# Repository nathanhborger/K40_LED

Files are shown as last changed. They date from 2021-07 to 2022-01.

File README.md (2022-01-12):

# K40_LED
LED Ring Origin Light for K40 Laser.
This device was designed with the intention to provide a solution to the K40's lack of origin detection/positioning.
Placed at the back of the laser, and reflected through two mirrors, the light will shine on the working peice, making a very distinct appearance which simplifies and enables the user to identify the exact locatin of the laser head.

## Schematic


## PCB Layout


## PCB
thumbnail_IMG_0565

## Parts List
| QTY | PART | NOTES |
|:---:|:----:|:-----:|
|8|LED XLAMP COOL WHITE 5000K 2SMD|https://cree-led.com/media/documents/XLampMX3.pdf|
|13|RES 13 OHM 1% 1/8W 0805||
|4|IC LED DRIVER LIN 1.5A 8SOPWRPAD|https://www.ti.com/general/docs/suppproductinfo.tsp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|
|1|LED DRIVER CC BUCK 2-52V 350MA|https://www.meanwellusa.com/upload/pdf/LDD-H/LDD-H-spec.pdf|
|4|RES SMD 1 OHM 1% 1/8W 0805||
|4|CAP CER 0.011UF 50V C0G/NP0 0805	||
|5|CAP CER 1UF 16V X7R 0805||
|1|RES SMD 51.1 OHM 1% 1/8W 0805||

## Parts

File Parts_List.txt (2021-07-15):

K40_LED_PARTS-LIST

12V 1A Supply:
https://www.amazon.com/R-Tech-UL-Listed-Switching-Supply-Adapter/dp/B00FEOB4EI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

LEDS:

RESISTOR:
https://www.digikey.com/en/products/detail/vishay-dale/CRCW0805200RJNEAHP/5326891

SWITCH:

VERSION 2:

RESISTOR[]
https://www.digikey.com/en/products/detail/stackpole-electronics-inc/RMCF0805JT18R0/1711894

LEDS[]
https://www.digikey.com/en/products/detail/samsung-semiconductor-inc/SPMWH1228FD5WATUS3/5959071

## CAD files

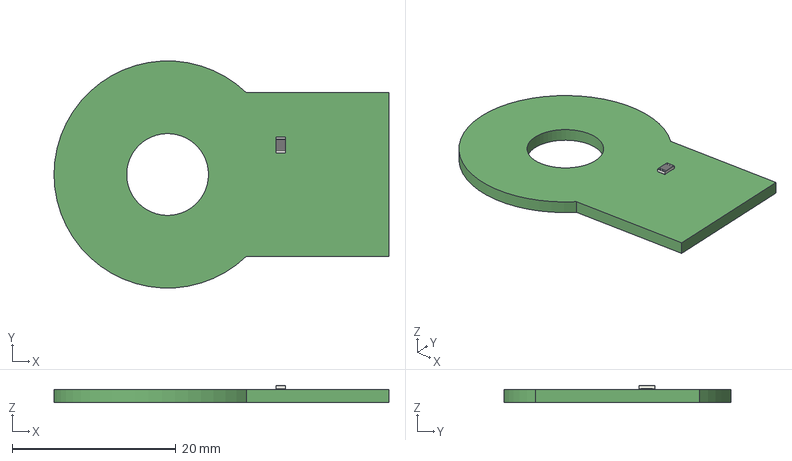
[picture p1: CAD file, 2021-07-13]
Fusion360_MODEL/K40-LED_PCB.step
41.0 x 27.7 x 2.10 mm

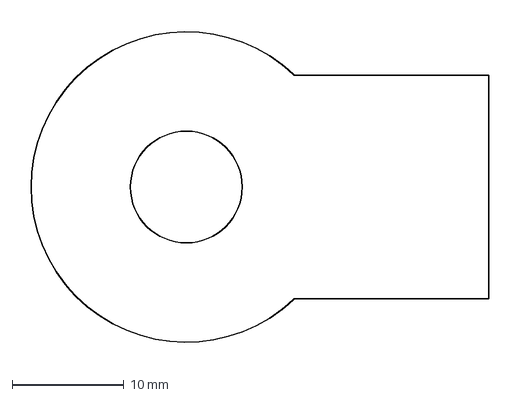
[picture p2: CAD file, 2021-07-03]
K40-LED_PCB/K40_LED_DXF.dxf
42.3 x 30.6 mm

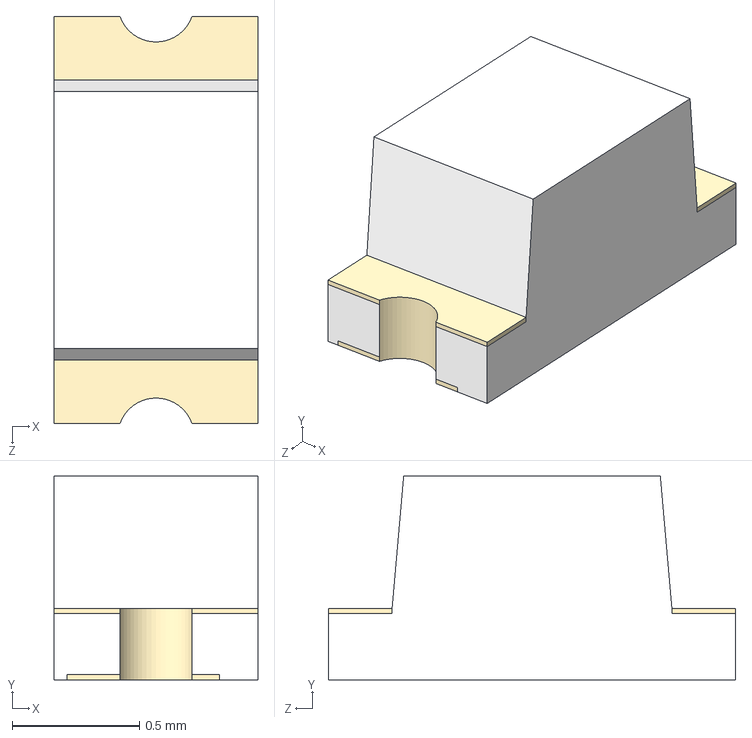
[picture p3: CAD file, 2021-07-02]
LRST-C190KGKT/LTST-C190KGKT.step
0.8 x 0.8 x 1.60 mm

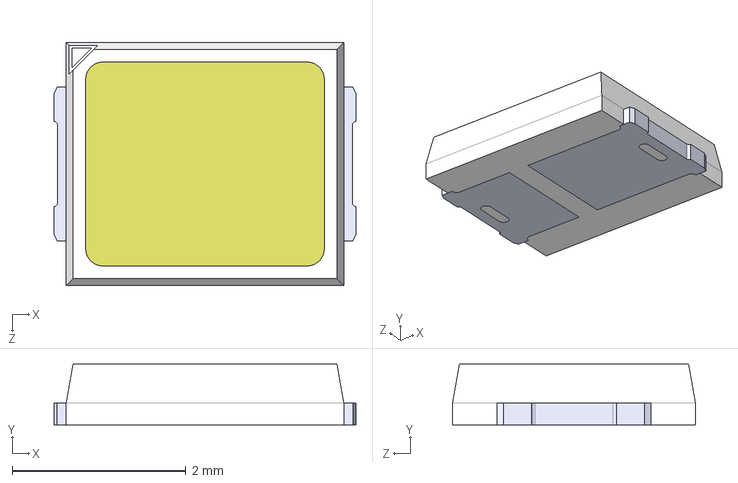
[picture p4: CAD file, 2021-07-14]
SPMWH1228FD5WATUS3_FOOTPRINT/LED_SPMWH1228FD5WARMSE.step
3.48 x 0.7 x 2.80 mm

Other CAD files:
K40-LED_PCB/K40_LED_DXF.dwg

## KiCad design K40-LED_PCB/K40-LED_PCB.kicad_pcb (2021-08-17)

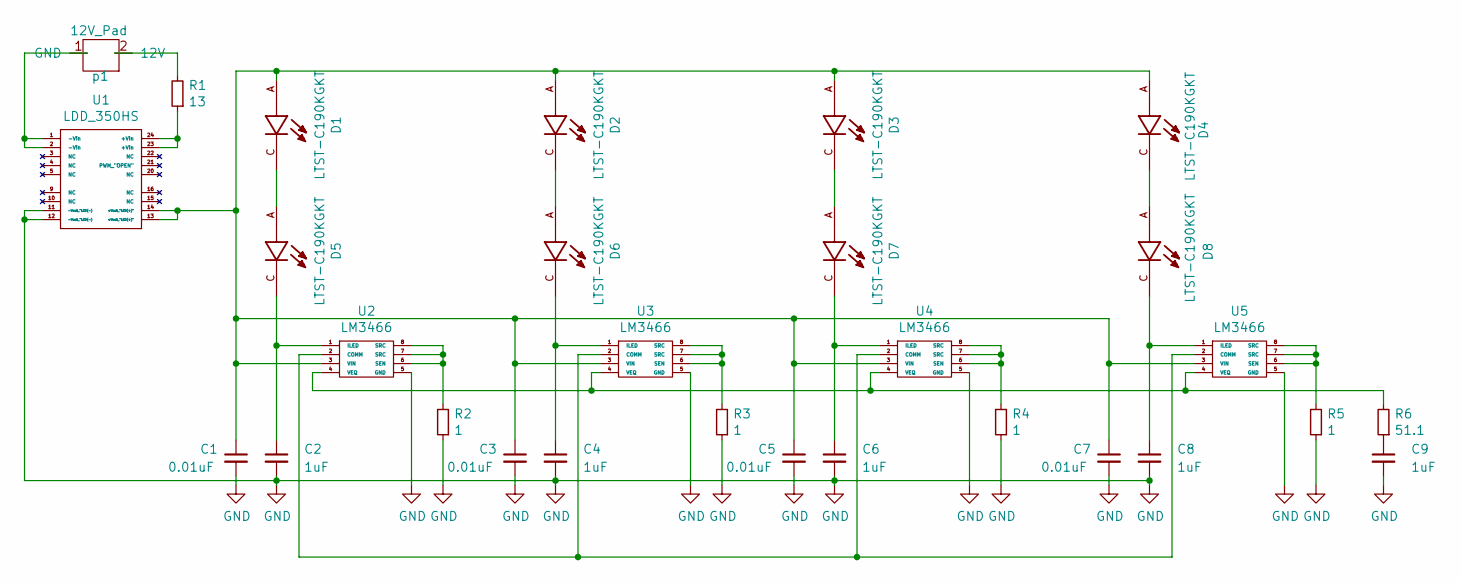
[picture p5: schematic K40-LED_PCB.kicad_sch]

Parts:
C1, C3, C5, C7: 0.01uF; C_0805_2012Metric
C2, C4, C6, C8, C9: 1uF; C_0805_2012Metric
D1, D2, D3, D4, D5, D6, D7, D8: LTST-C190KGKT; Cree_MX3AWT-A1-R250-000BE3
R1: 13; R_0805_2012Metric
R2, R3, R4, R5: 1; R_0805_2012Metric
R6: 51.1; R_0805_2012Metric
U1: LDD_350HS; LDD-350HS
U2, U3, U4, U5: LM3466; NOPB
p1: 12V_Pad; 12V_Through_Hole

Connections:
GND: C1.2, C2.2, C3.2, C4.2, C5.2, C6.2, C7.2, C8.2, C9.2, D1.65, D2.65, D3.65, D4.65, D5.65, D6.65, D7.65, D8.65, R2.1, R3.1, R4.1, R5.1, U1.11 (-Vout_"LED(-)), U1.12 (-Vout_"LED(-)), U2.5 (GND), U2.9, U3.5 (GND), U3.9, U4.5 (GND), U4.9, U5.5 (GND), U5.9
unnamed: C1.1, C3.1, C5.1, C7.1, D1.A, D2.A, D3.A, D4.A, U1.13 (+Vout_"LED(+)"), U1.14 (+Vout_"LED(+)"), U2.3 (VIN), U3.3 (VIN), U4.3 (VIN), U5.3 (VIN)
unnamed: C2.1, D5.C, U2.1 (ILED)
unnamed: C4.1, D6.C, U3.1 (ILED)
unnamed: C6.1, D7.C, U4.1 (ILED)
unnamed: C8.1, D8.C, U5.1 (ILED)
unnamed: C9.1, R6.1
unnamed: D1.C, D5.A
unnamed: D2.C, D6.A
unnamed: D3.C, D7.A
unnamed: D4.C, D8.A
unnamed: R1.1, U1.23 (+Vin), U1.24 (+Vin)
unnamed: R1.2, p1.2 (12V)
unnamed: R2.2, U2.6 (SEN), U2.7 (SRC), U2.8 (SRC)
unnamed: R3.2, U3.6 (SEN), U3.7 (SRC), U3.8 (SRC)
unnamed: R4.2, U4.6 (SEN), U4.7 (SRC), U4.8 (SRC)
unnamed: R5.2, U5.6 (SEN), U5.7 (SRC), U5.8 (SRC)
unnamed: R6.2, U2.4 (VEQ), U3.4 (VEQ), U4.4 (VEQ), U5.4 (VEQ)
unnamed: U1.1 (-Vin), U1.2 (-Vin), p1.1 (GND)
unnamed: U2.2 (COMM), U3.2 (COMM), U4.2 (COMM), U5.2 (COMM)

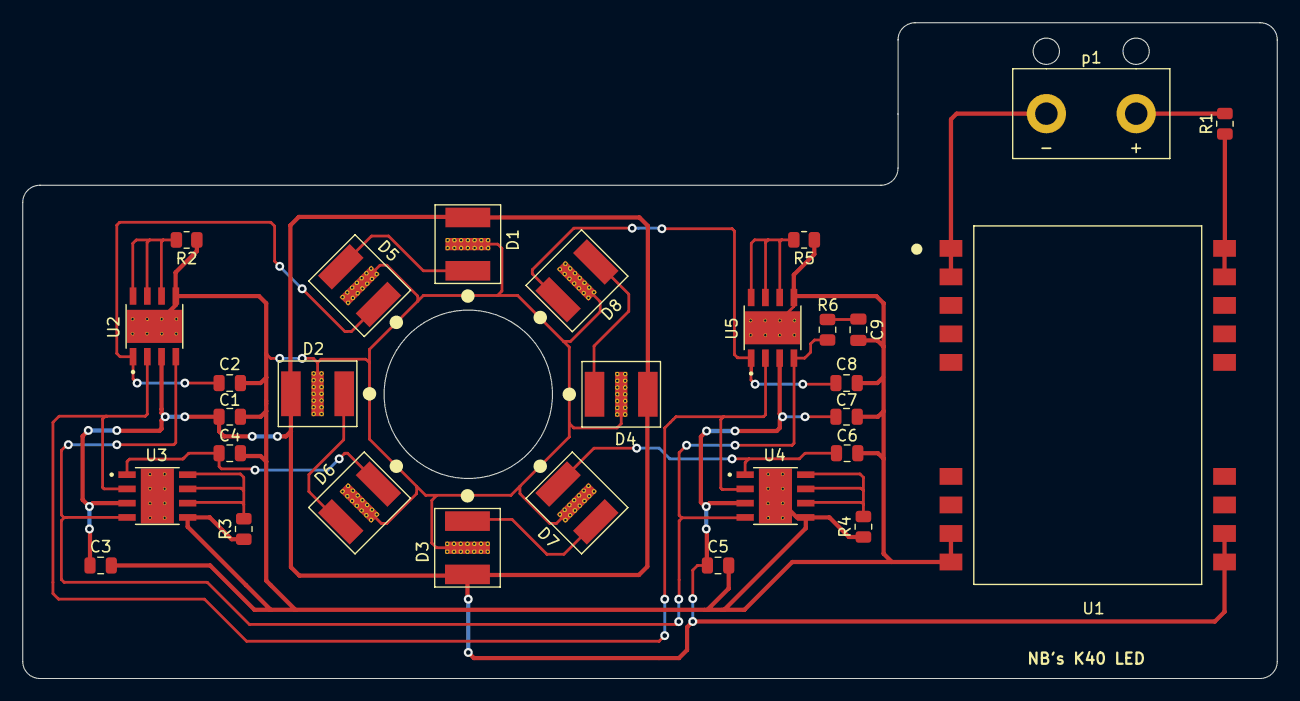
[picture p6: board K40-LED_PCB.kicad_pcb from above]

Board: 2 copper layers, 111.8 x 58.4 mm, 29 parts (0 on the bottom side), 20 nets.

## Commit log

2021-07-02 Folders Added
    [K40-LED_PCB.kicad_pcb, K40-LED_PCB.sch, LTST-C190KGKT.step]
2021-07-02 Schmatic Update
    [K40-LED_PCB.sch]
2021-07-03 Added Gerber
    [K40-LED_PCB-B_Cu.gbl, K40-LED_PCB-B_Mask.gbs, K40-LED_PCB-B_SilkS.gbo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]
2021-07-13 Added Step files
    [K40-LED_PCB.step]
2021-07-14 Added new led footprint
    [LED_SPMWH1228FD5WARMSE.step]
2021-07-14 Connect symbol to new footprint
    [K40-LED_PCB.sch]
2021-07-14 Trace deletion
    [K40-LED_PCB.kicad_pcb]
2021-07-15 more footprints
2021-07-15 Symbol Changes
    [K40-LED_PCB.sch]
2021-07-15 More Footprint updates
    [K40-LED_PCB.kicad_pcb, K40-LED_PCB.sch]
2021-07-17 Footprint updates
    [K40-LED_PCB.sch]
2021-07-17 updated more footprints
2021-07-17 removed old footprint associations
    [K40-LED_PCB.kicad_pcb]
2021-07-18 Major PCB Changes
    [K40-LED_PCB.sch]
2021-07-18 PCB_Changes + footprints
    [K40-LED_PCB.kicad_pcb, K40-LED_PCB.sch]
2021-07-18 More circular changes correct
    [K40-LED_PCB.kicad_pcb]
2021-07-18 PCB Cathode traces
    [K40-LED_PCB.kicad_pcb, K40-LED_PCB.sch]
2021-07-18 Cont Traces
    [K40-LED_PCB.kicad_pcb]
2021-07-18 More_PCB Updates LM3466 movementr
    [K40-LED_PCB.kicad_pcb]
2021-07-18 More PCB Updates
    [K40-LED_PCB.kicad_pcb]
2021-07-18 Updated more PCB
    [K40-LED_PCB.kicad_pcb]
2021-07-18 Updated PCB Again
    [K40-LED_PCB.kicad_pcb]
2021-08-07 Lots of updates on the K40 LED
    [K40-LED_PCB-B_Cu.gbl, K40-LED_PCB-B_Mask.gbs, K40-LED_PCB-B_Silkscreen.gbo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]
2021-08-07 Thermal Reliefs updated
    [K40-LED_PCB.kicad_pcb]
2021-08-07 More Thermal Pad Updates
    [K40-LED_PCB.kicad_pcb]
2021-08-08 More Thermal Upgrades and Progression
    [K40-LED_PCB.kicad_pcb]
2021-08-08 D8 Thermal Updates
    [K40-LED_PCB.kicad_pcb]
2021-08-08 D8 Thermal Upgrades
    [K40-LED_PCB.kicad_pcb]
2021-08-08 Continued Upgrades to Thermal Pads
    [K40-LED_PCB.kicad_pcb]
2021-08-08 Upgraded Thermal Relief
    [K40-LED_PCB.kicad_pcb]
2021-08-08 Grounding Thermal Relief Pads
    [K40-LED_PCB.kicad_pcb]
2021-08-08 Continued Updates On Thermal
    [K40-LED_PCB.kicad_pcb]
2021-08-08 Thermals Completed to Ground
    [K40-LED_PCB.kicad_pcb]
2021-08-17 updated k40 led
    [K40-LED_PCB-B_Cu.gbl, K40-LED_PCB-B_Mask.gbs, K40-LED_PCB-B_Silkscreen.gbo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]
2022-01-12 Added Physical Circuit Image
2023-12-10 Initial Upgrades to recent KiCAD
